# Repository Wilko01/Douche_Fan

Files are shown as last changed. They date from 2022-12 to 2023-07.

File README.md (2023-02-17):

# Fan bathroom
This ESP32 controls the fan of the badroom and is it also might look right and just because I can I added lights to the fan. The fan is an in-line fan, where the cover in the bathroom itself is just for providing a nice cover for the 120mm airgap.

## Description and operation instructions
The fan is turned on when a certain humidity is detected and turned off when it is below another humidity value. The fan is controlled via different levels where at lower humidity levels the fan runs at a lower speed and when the hunidity level is high the fan runs at a higher speed. The fan is also turned on when the temperature is very high. The logic is running on the ESP32, so even if HomeAssistant is down the fan operates independently. To be able to override the logic there is an override variable which enables remote control and bypasing the ESP32 fan control.
The LEDs are just for fun and can be controlled manually or like in my case via HomeAssistant where some logic is in NodeRed to control the LEDs.

 ## Technical description
The PWM fan is controlled via the PWM signal coming from the ESP32. The ESP32 is running ESPHOME and connected to Home Assistant. The sensor for the humidity is included in this module, the LEDs of the fan are connected to this ESP32, but they only can be contolled via Home Assistant and an external motio sensor.
The construction is made modular to enable easy printing and mounting. I used magnets to easily remove parts, not only for mounting, but also for cleaning. The fan fits a 120mm pipe. 

## The results
The fan in the bathroom

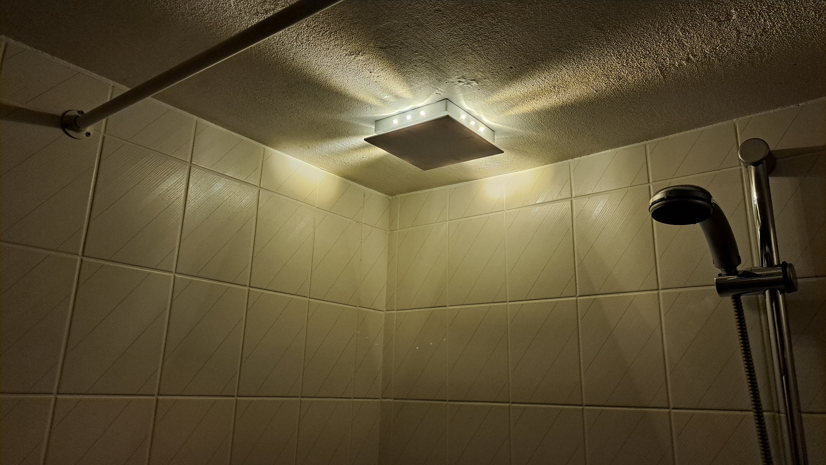
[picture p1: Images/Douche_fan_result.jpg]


The ESP controlling the fan and the LEDs

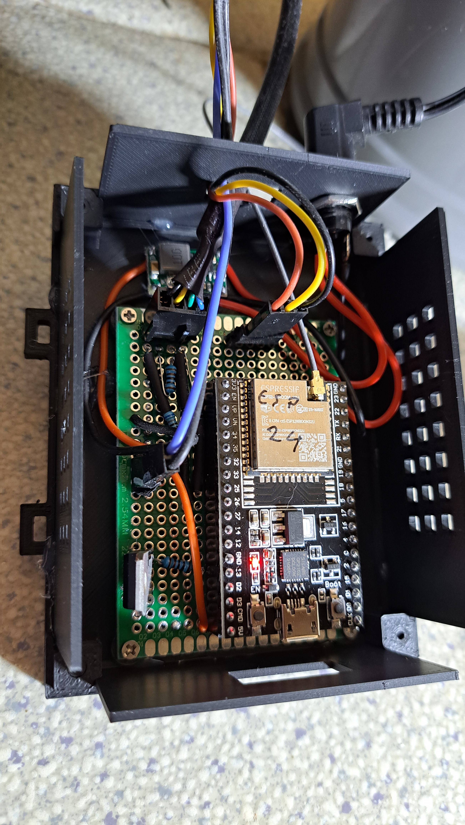
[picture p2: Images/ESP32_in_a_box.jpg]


The fan in line with the ESP

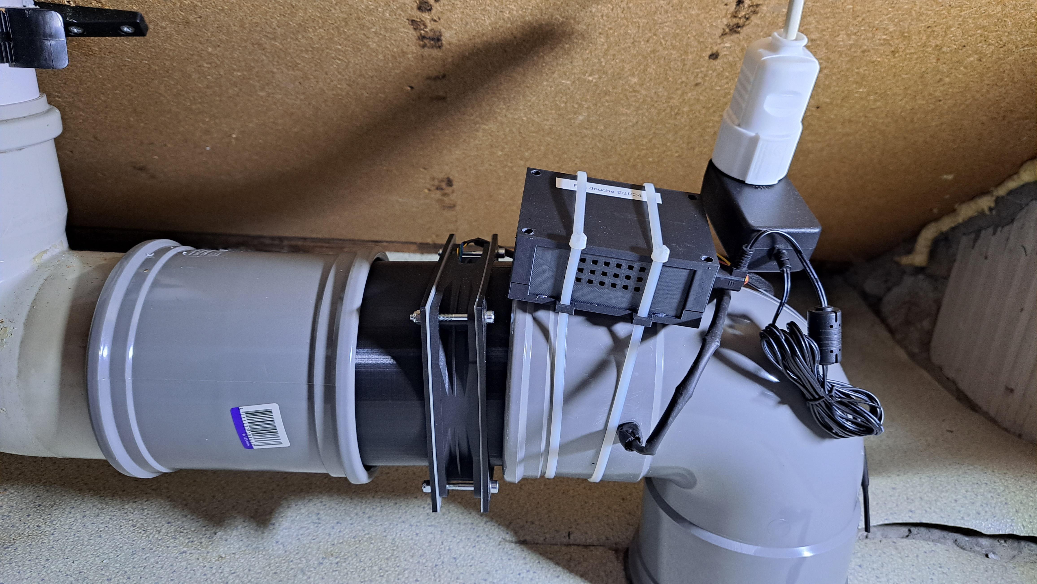
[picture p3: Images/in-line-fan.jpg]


## Parts
1 x ESP32

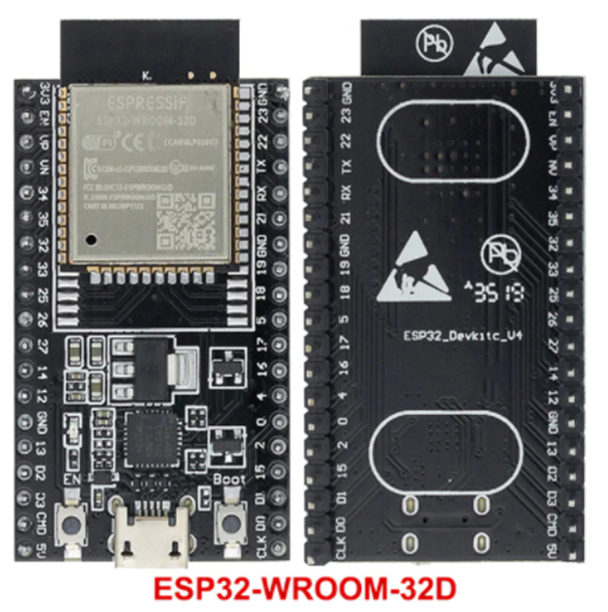
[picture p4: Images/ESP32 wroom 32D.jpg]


1 x DHT22 or AM2302

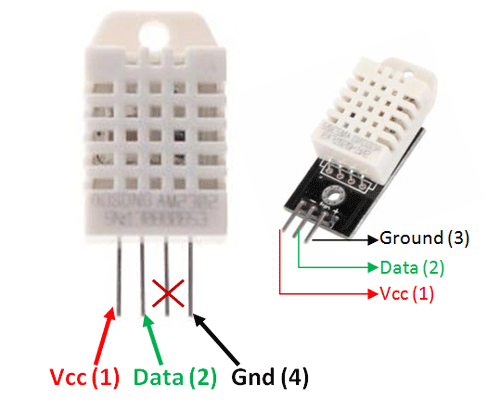
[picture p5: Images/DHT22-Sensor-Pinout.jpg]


1 x DHT22 or AM2302 vs DHT11

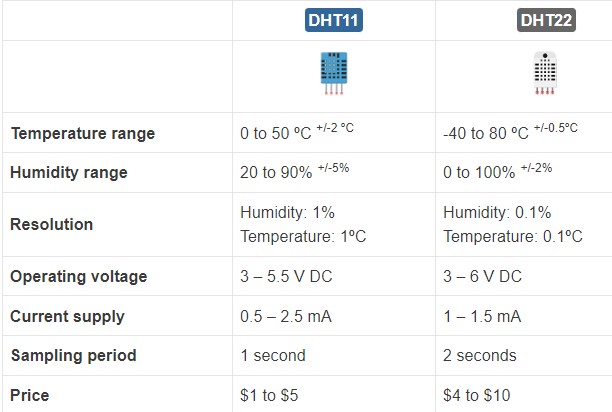
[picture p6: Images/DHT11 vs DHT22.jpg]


1 x Fan NF-F12 IP2000-67 Noctua NF-F12 industrialPPC-2000 IP67, 120mm

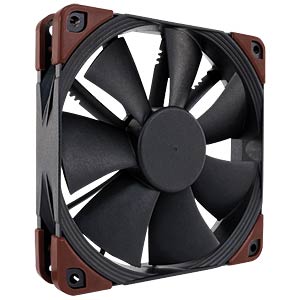
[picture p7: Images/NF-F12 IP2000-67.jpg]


Fan pinout pinout

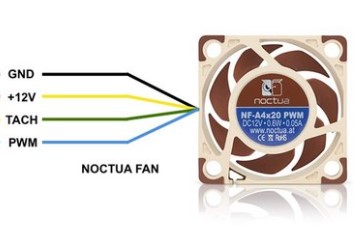
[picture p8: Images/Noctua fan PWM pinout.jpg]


1 x Mini360 DC- DC buck converter

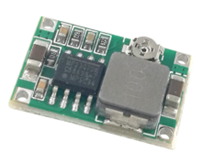
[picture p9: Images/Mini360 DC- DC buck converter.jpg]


Resistors
1 x 180 0,25W
1 x 680 0,25W
3 x 1k 0,25W
1 x 4k7 0,25W
4 x 33 0,5W

1 x TIP120 Darlington transistor

11 x LED warm white 5mm

1 x 5.5 x 2.1 connector

1 x 12V DC adapter

60cm heatshrink tube to group the wires running thru the fan pipes

Some small screws

2 x M2 x 6 mm

2 x M2 x 8 mm

For the piping use 120 pipes to fit your needs

### Schematic overview
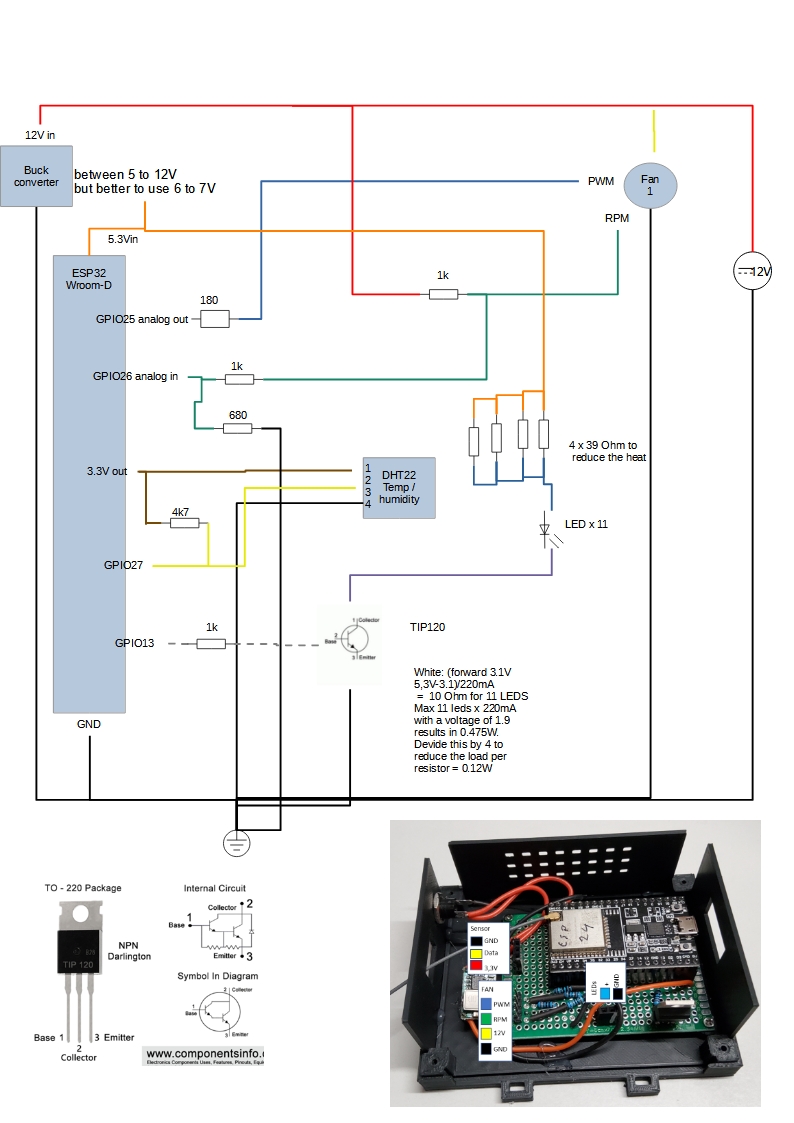
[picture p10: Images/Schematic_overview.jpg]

 
Connector connections overview

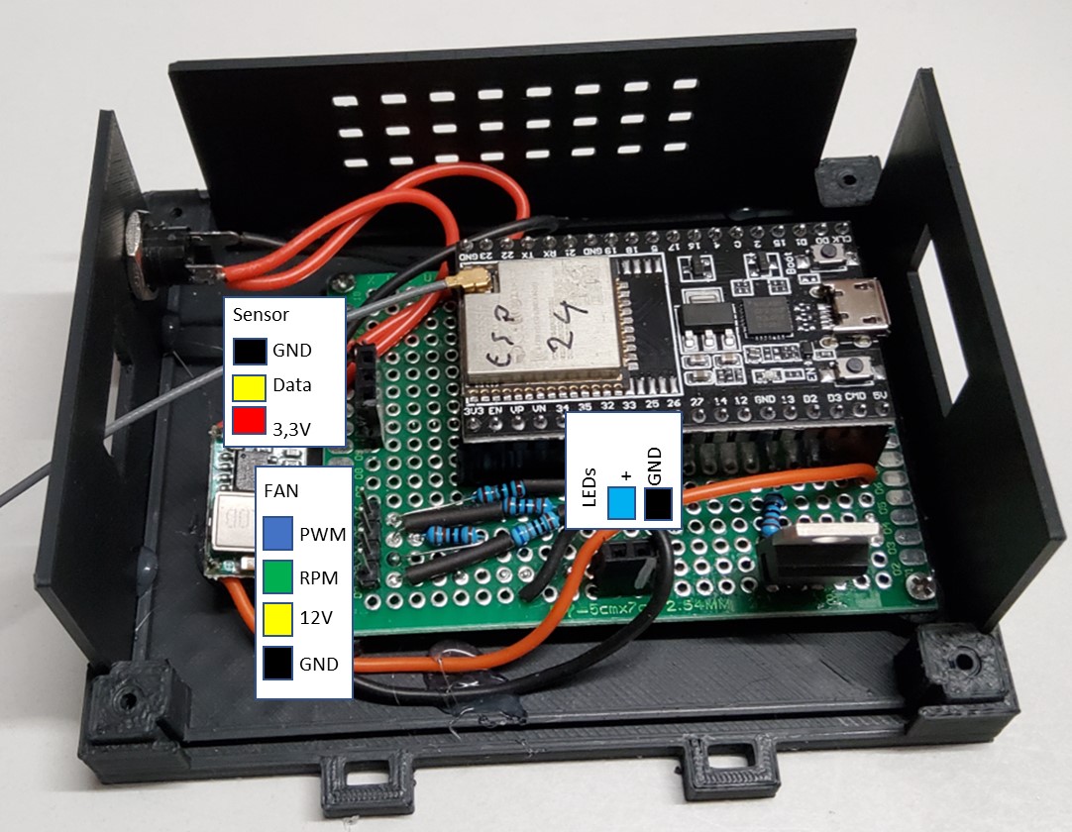
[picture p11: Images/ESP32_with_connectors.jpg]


Power the circuit only via 12V and run code updates via OTA and ESPHOME.

### ESPHOME Configuration
### ESPHome Configuration in Home Assistant
Create a new ESPHOME device with this code:
## Code
[Code in ESPHOME](code.vbs)

## 3D printer files
[3D Printer files](3D_Printer_Files)
#### ESP box

1 x ESP bottom 01.stl

1 x ESP Top 01.stl

2 x ESP side long 01.stl

1 x ESP side short cables in 01.stl

1 x ESP side short USB side 01.stl

#### Bathroom cover
1 x Inner fan ceiling mount cover 02 curved edges yellow 1mm.stl

1 x Inner fan ceiling mount cover matching the loose pipe model 04.stl

1 x Inner fan ceiling mount loose pipe model 02.stl

1 x Inner fan ceiling mount loose pipe of loose pipe model 02.stl

#### 120mm connections in the pipes
1 x Connection fan 03.stl

1 x Connection fan extended 01.stl

2 x Seal for fan 01.stl  to connect between the fan and the 3D printed parts

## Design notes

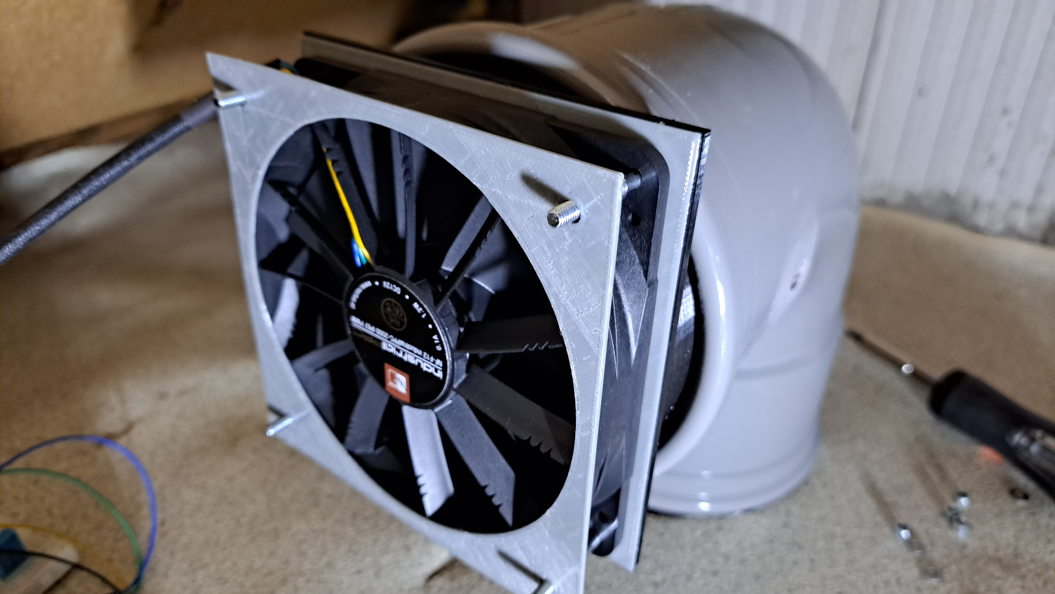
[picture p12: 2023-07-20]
Images/in-line-fan02.jpg

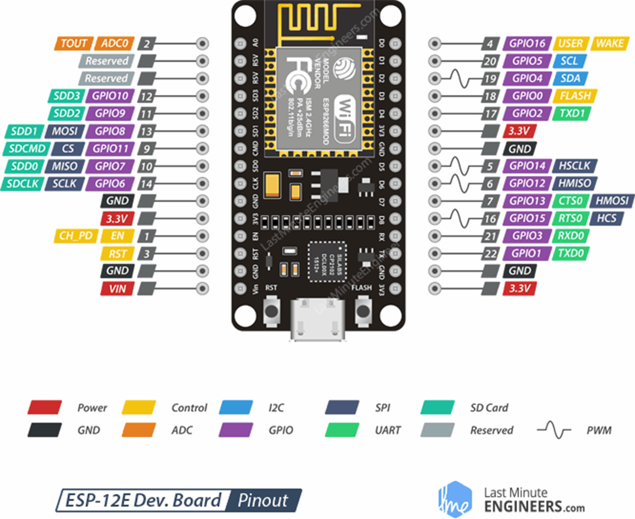
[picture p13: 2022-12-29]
Images/ESP8266_NodeMCU.jpg

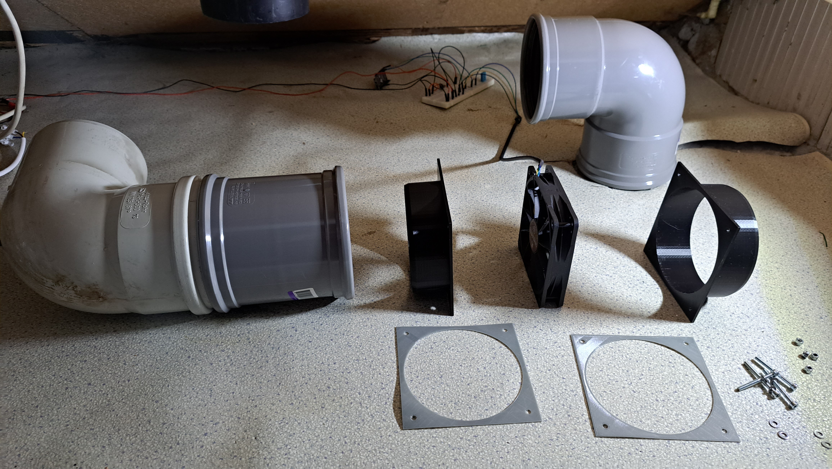
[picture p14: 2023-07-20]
Images/in-line-fan03.jpg

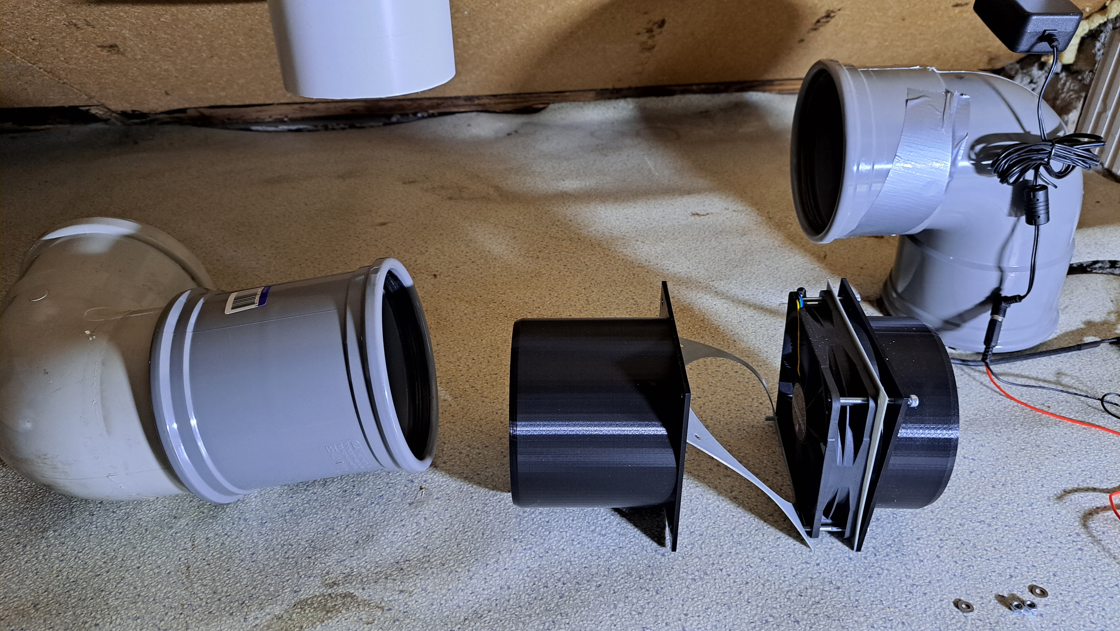
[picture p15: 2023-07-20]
Images/In-line_fan01.jpg

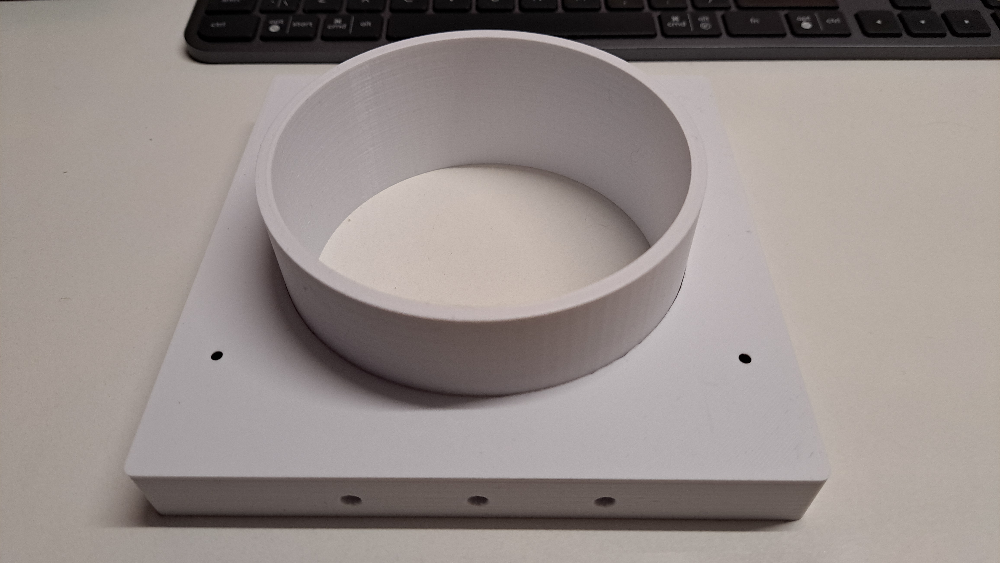
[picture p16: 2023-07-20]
Images/Fan_cover02.jpg

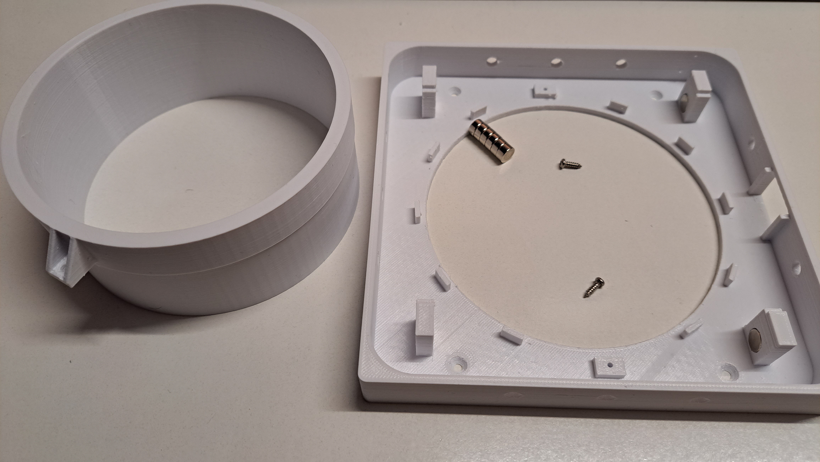
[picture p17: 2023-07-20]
Images/Fan_cover03.jpg

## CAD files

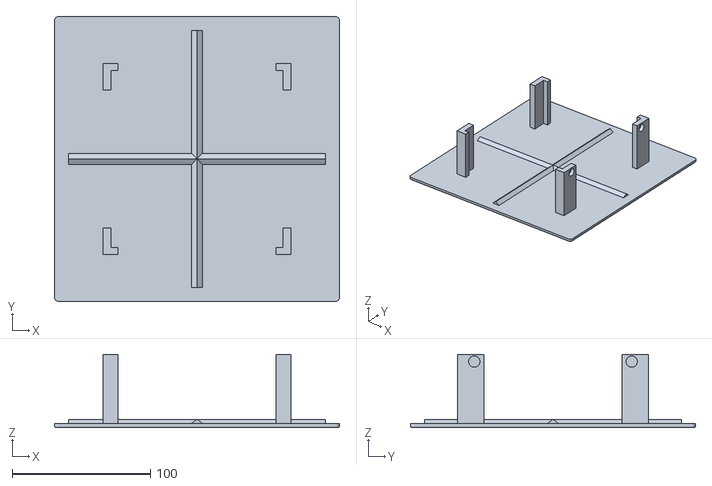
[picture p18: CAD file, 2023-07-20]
3D_Printer_Files/Inner fan ceiling mount cover 03 curved edges yellow 1mm.stl
206.4 x 206.4 x 53.0

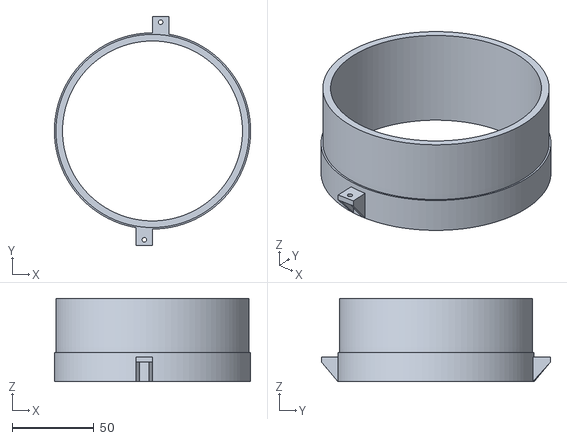
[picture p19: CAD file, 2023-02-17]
3D_Printer_Files/Inner fan ceiling mount loose pipe of loose pipe model 02.stl
120.0 x 140.0 x 51.0

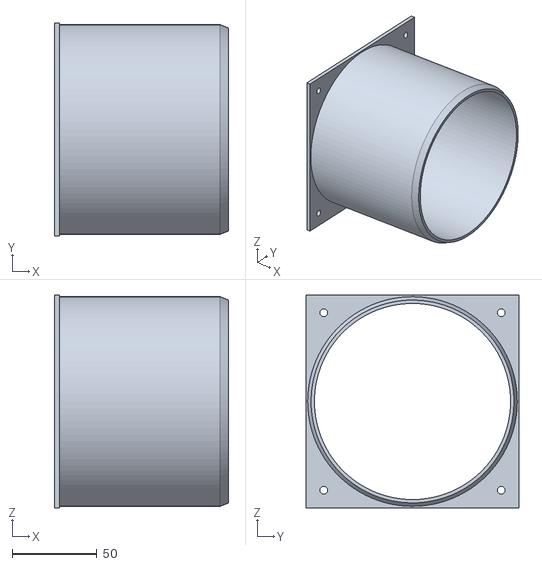
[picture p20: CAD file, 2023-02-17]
3D_Printer_Files/Connection fan extended 01.stl
103.0 x 126.0 x 126.0

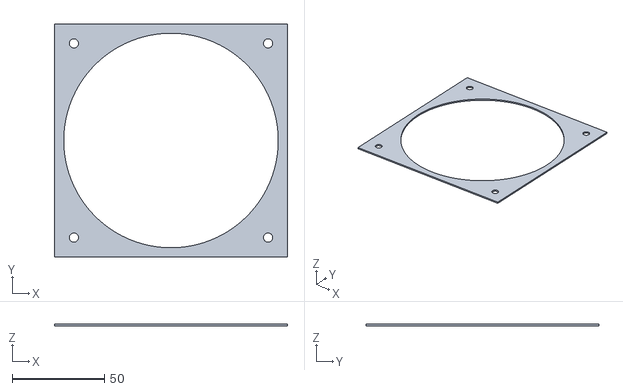
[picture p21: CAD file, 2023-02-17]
3D_Printer_Files/Seal for fan 01.stl
126.0 x 126.0 x 1.00

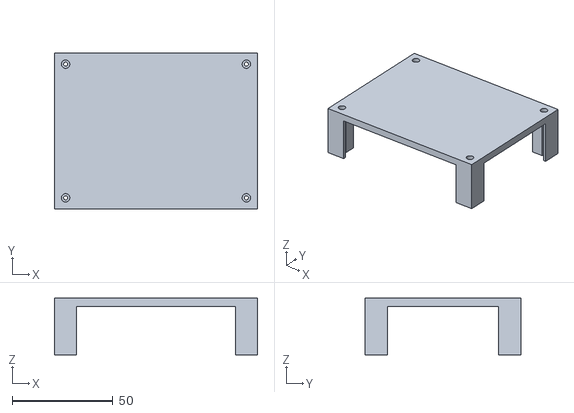
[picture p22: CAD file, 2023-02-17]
3D_Printer_Files/ESP Top 01.stl
100.5 x 77.2 x 28.0

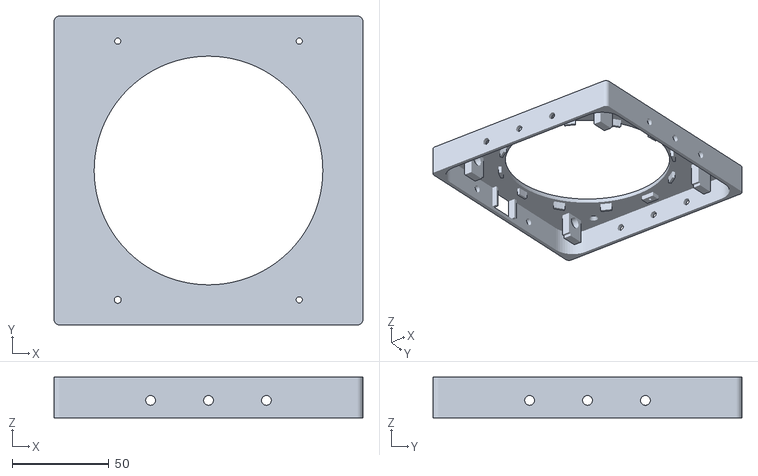
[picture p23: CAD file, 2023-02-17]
3D_Printer_Files/Inner fan ceiling mount loose pipe model 02.stl
160.0 x 160.0 x 21.0

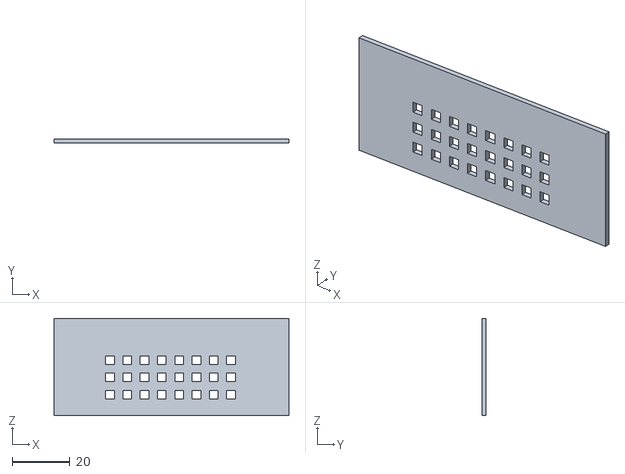
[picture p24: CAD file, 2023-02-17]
3D_Printer_Files/ESP side long 01.stl
81.5 x 1.50 x 33.8

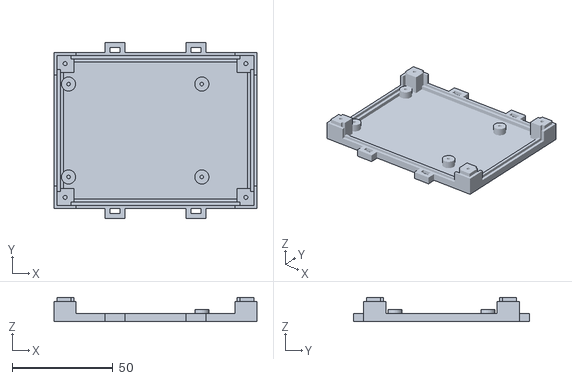
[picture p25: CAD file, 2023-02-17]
3D_Printer_Files/ESP bottom 01.stl
100.5 x 87.2 x 12.0

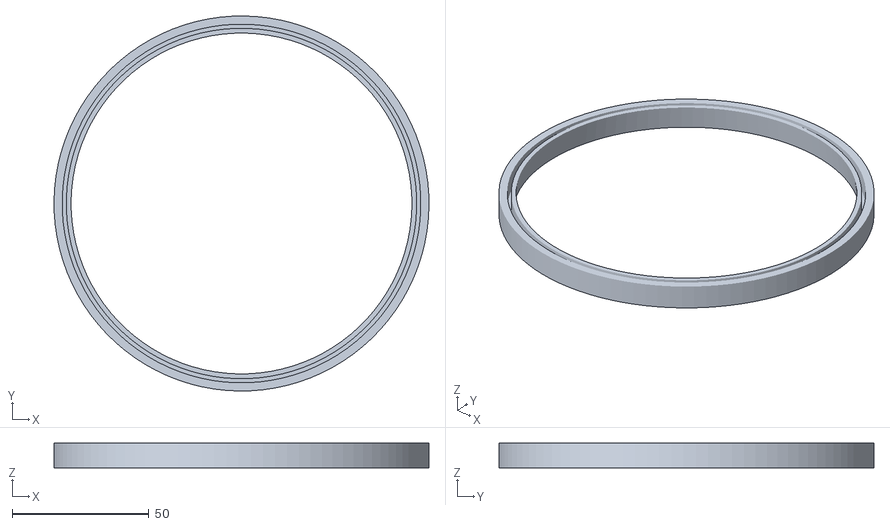
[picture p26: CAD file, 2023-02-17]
3D_Printer_Files/Ring TPU 02.stl
137.0 x 137.0 x 9.00

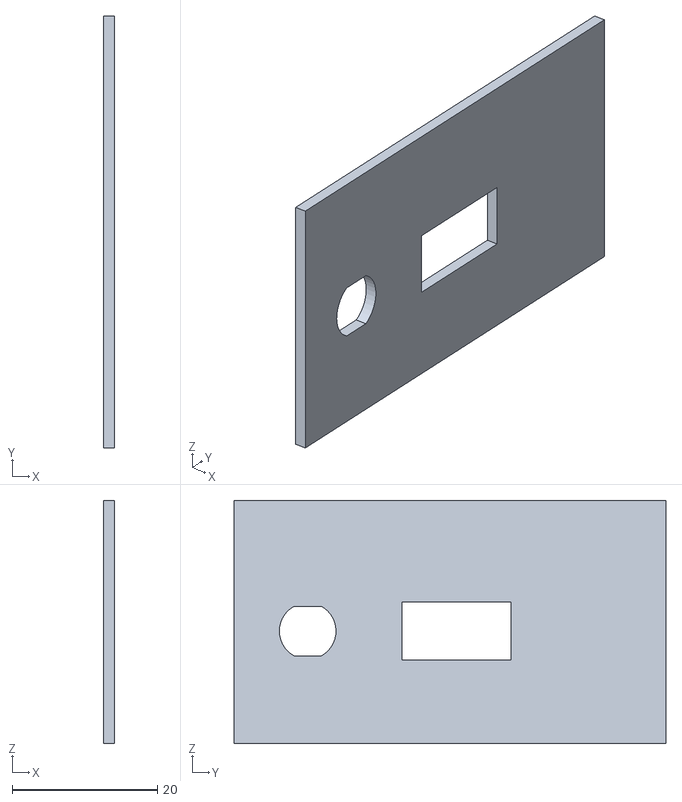
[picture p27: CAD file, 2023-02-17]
3D_Printer_Files/ESP side short cables in 01.stl
1.50 x 59.5 x 33.5

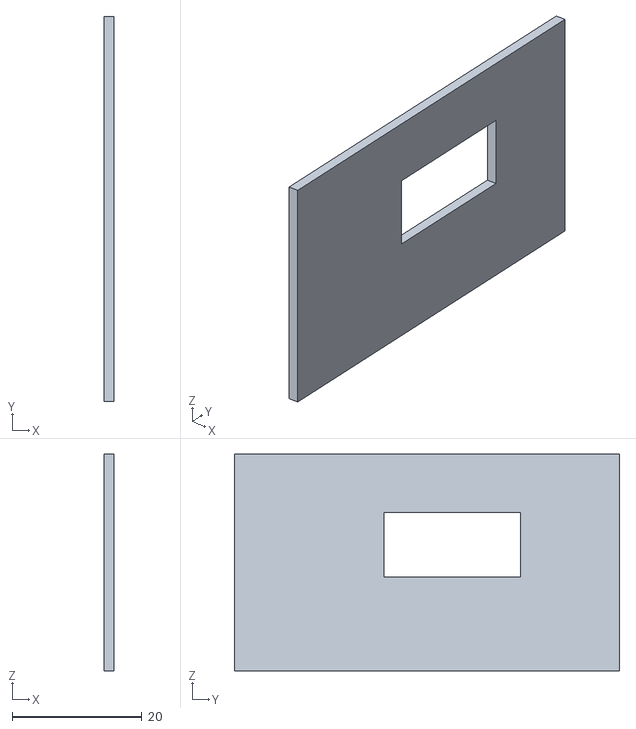
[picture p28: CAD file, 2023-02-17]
3D_Printer_Files/ESP side short USB side 01.stl
1.50 x 59.5 x 33.5

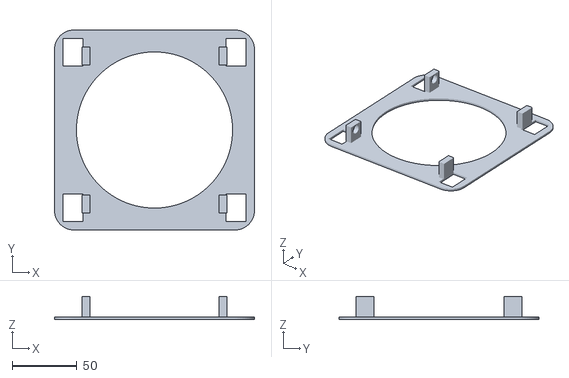
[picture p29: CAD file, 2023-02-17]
3D_Printer_Files/Inner fan ceiling mount cover matching the loose pipe model 04.stl
154.0 x 154.0 x 18.0

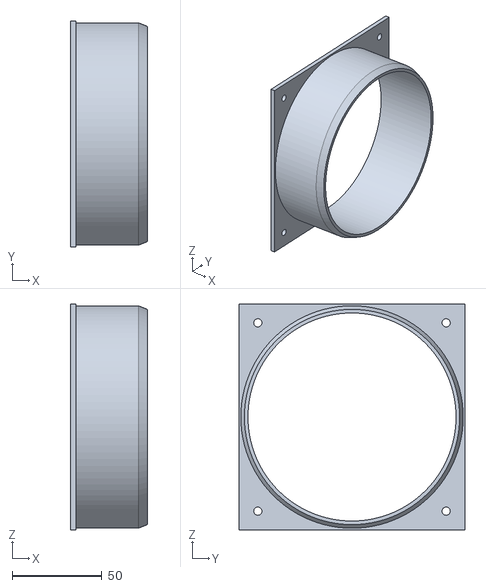
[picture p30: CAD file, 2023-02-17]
3D_Printer_Files/Connection fan 03.stl
43.0 x 126.0 x 126.0

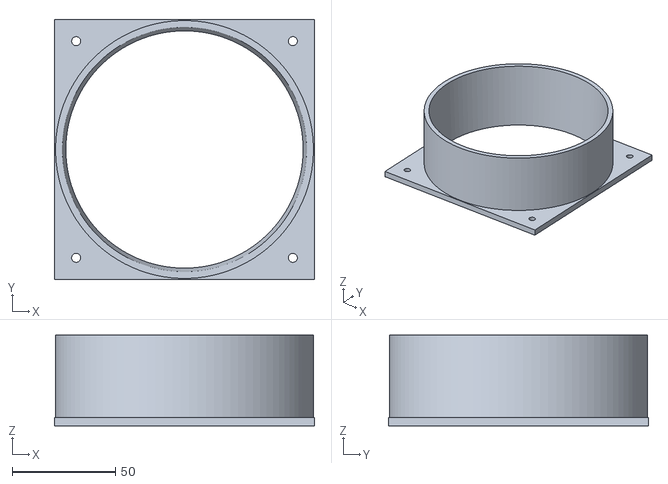
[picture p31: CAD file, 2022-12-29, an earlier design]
3D_Printer_Files/Old/Connection fan 01.stl
126.0 x 126.0 x 44.0

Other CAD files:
3D_Printer_Files/Old/Fan douche 01.skp
3D_Printer_Files/Old/Fan douche 02.skp
3D_Printer_Files/Old/Fan douche 03.skp

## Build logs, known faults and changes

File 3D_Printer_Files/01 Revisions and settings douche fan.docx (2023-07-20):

# Print settings:

- Print material: PLA and TPU
- Rotation of the objects: No comment.
- Support: No
- Skirt, brim: Skirt.
- Infill: 50% for PLA and 20% for TPU
- Print the ‘Inner fan ceiling mount 01’ with the side of the pipe connection at the building plate so the parts where the magnets are located doesn’t need support.

# Additional instructions

- None

# Materials needed

- Filament. Started with ABS, but the adhesive between the layers of the used ABS was not strong and therefore switched to PLA
- 4 x Bolt M4 x 40 or 8 x M4 x 15
- 4 x Lock nuts M4 or 8 when using M4 x 15

# Log history

# Version 0.12

- Increased the airgap to have a better flow. Extended the legs of ‘Inner fan ceiling mount cover 03’ by 22mm and widened the sides with 10mm on all sides so the chance of looking into the gap is reduced

# Version 0.11

- Added the box for the ESP
  - ESP bottom 01
  - ESP Top 01
  - ESP side short cables in 01
  - ESP side short USB side 01
  - ESP side long 01

# Version 0.10

- ‘Inner fan ceiling mount cover matching the loose pipe model 03’ added magnets to mount the cover to the main part. This could be solved differently, by adding fix positions at the ‘Inner fan ceiling mount loose pipe model’ and use screws to connect. As my part was already printed I needed to reprint or adjust the cover. I chose to change the cover.
- After test printing the fitting between the cover and the other parts was too tight. Therefor the gaps were extended

# Version 0.9

- ‘Inner fan ceiling mount cover 02’ made the material around the magnet 2mm wider
- ‘Inner fan ceiling mount cover matching the loose pipe model 02’ made the material around the magnet 2mm wider
- ‘Inner fan ceiling mount cover matching the loose pipe model 02’ made the material around the magnet 2mm wider
- ‘Inner fan ceiling mount loose pipe model 02’ made the material around the magnet 2mm wider and enlarged the connection to the tube by 0.2mm
- Changed the material from ABS to PLA as the ABS doesn’t deliver a solid layer for both test prints of ‘Inner fan ceiling mount loose pipe model 02’ and the pipe
- ‘Inner fan ceiling mount loose pipe of loose pipe model 02’ enlarged to snug fit better the outer diameter to 59.05 mm
- ‘Inner fan ceiling mount loose pipe model 02’ Removed the holes in the outer rim as they will not fit with the old holes in the concrete

# Version 0.8

- ‘Inner fan ceiling mount 02’ adjusted the mounting holes to fit the available M2.9x25mm screws
- Added additional mounting holes for the case that the outer mounting holes will not fit. Inner fan ceiling mount loose pipe model 02’
- Added a new model which makes the printing easier and future upgrades. The pipe fitting into the 125mm pipe (‘Inner fan ceiling mount loose pipe model 01’ ) is now a separate part which will be screwed upon the ‘Inner fan ceiling mount loose pipe model 01’.
- Modified the ‘Inner fan ceiling mount cover matching the loose pipe model 01’

# Version 0.7

- ‘Inner fan ceiling mount 02’ Moved the cable guidance gap to the other side to ensure a shorter path
- ‘Inner fan ceiling mount 03’ adjusted the diameter of the 62mm circle to fit it into the 62,5mm wide pipe. The width of the pipe is 3mm, hence this part needs to fit in
- Added cover ‘Inner fan ceiling mount cover 01’

# Version 0.6

- Added ‘Connection fan extended 01’ to fit the new dakdoorvoer.

# Made

# Version 0.5

- Added ‘Inner fan ceiling mount cover 01’
- Made small adjustments to ‘Inner fan ceiling mount 02’

# Version 0.4

- Added ‘Inner fan ceiling mount 01’

# Added ‘ring TPU

# Version 0.3

- Added ‘air valve 01’
- Added ‘ring TPU 02’ for in the 125mm 90 degree curve which doesn’t have a rubber closing ring
- Added ‘seal for fan’.
- ‘Connection fan 03’ and ‘Connection fan 03 with straith end at circle’ Made the holes for the bolts wider for a better fit to 2.3mm

# Version 0.2

- The ‘Connection fan 01’ fitted too tight and broke the circle from the base when removing from the 90’ curve. Reduced the diameter from 62,5 to 62mm
- Made the last part of the circle slightly curved to the inside to ensure an easier slide in.

# Version 0.1

- First release

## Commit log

2023-07-20 updated led resistors
    [Inner fan ceiling mount cover 02 curved edges yellow 1mm.stl, Inner fan ceiling mount cover 03 curved edges yellow 1mm.stl]
2023-08-19 added restart button
